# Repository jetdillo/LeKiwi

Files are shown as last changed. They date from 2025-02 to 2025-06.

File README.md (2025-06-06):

# LeKiwi
<div style="display: flex; justify-content: center; align-items: center; padding: 25px;">
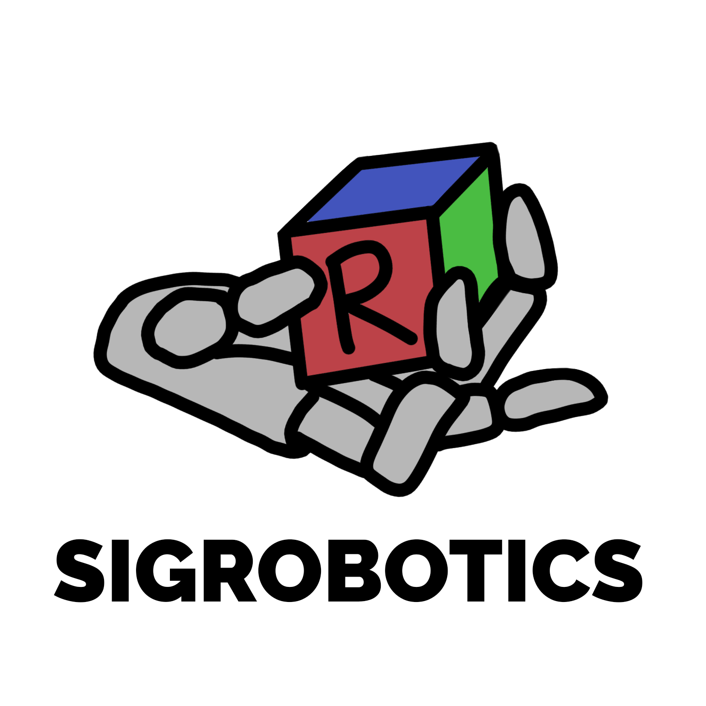
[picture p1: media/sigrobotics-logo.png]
    
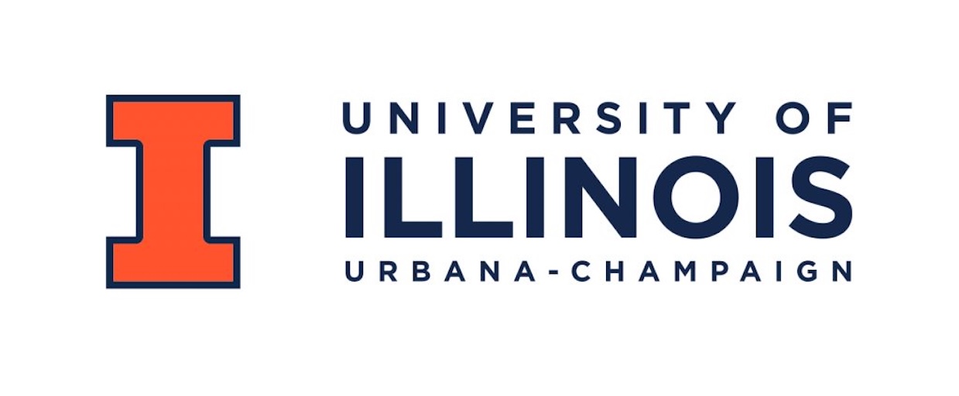
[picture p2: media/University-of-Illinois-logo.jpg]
    
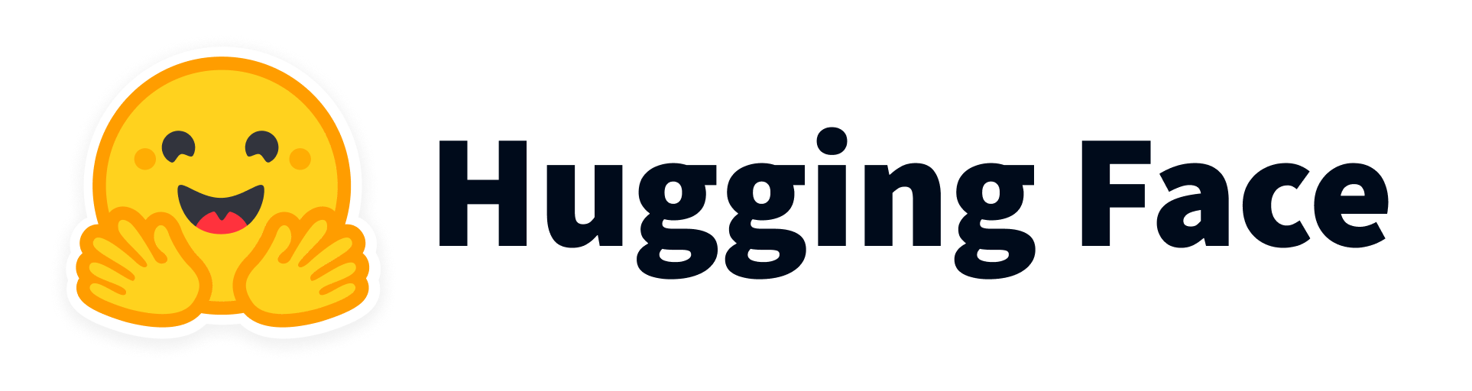
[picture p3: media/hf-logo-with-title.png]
    
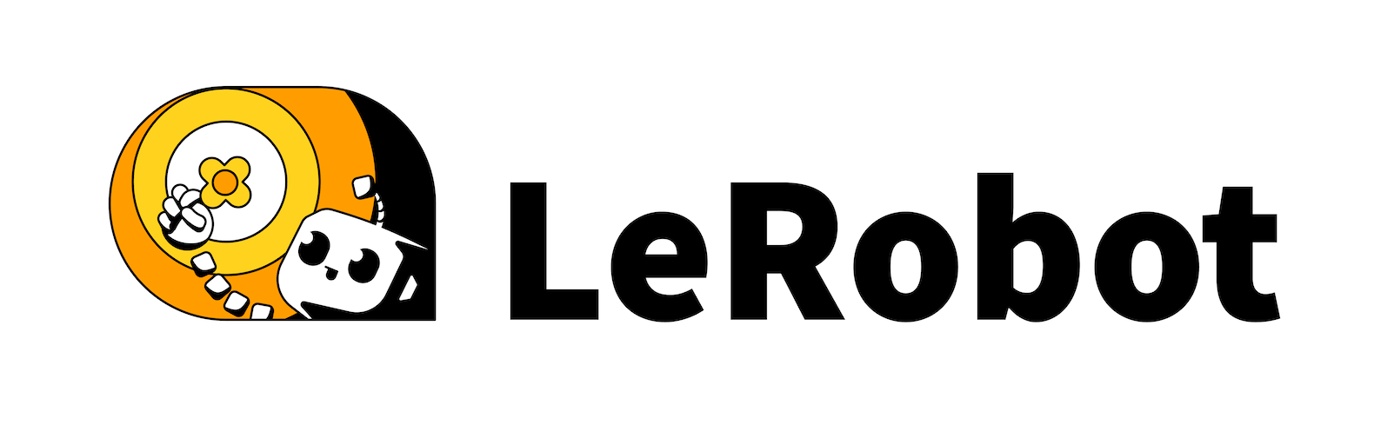
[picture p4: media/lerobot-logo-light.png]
    
</div>

> LeKiwi - Low-Cost Mobile Manipulator | Version 1

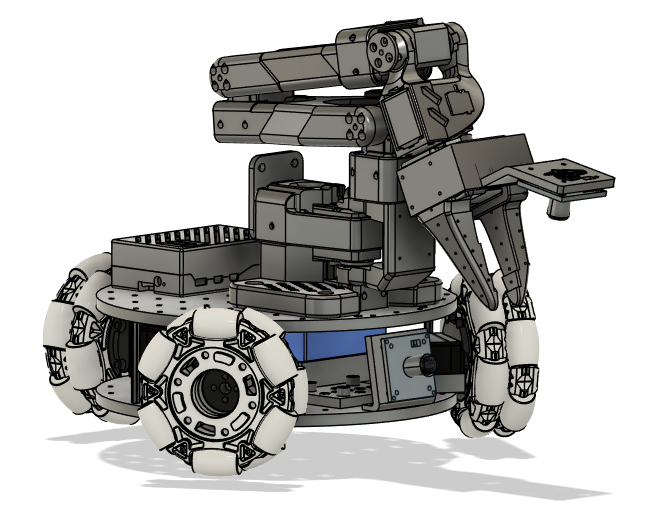
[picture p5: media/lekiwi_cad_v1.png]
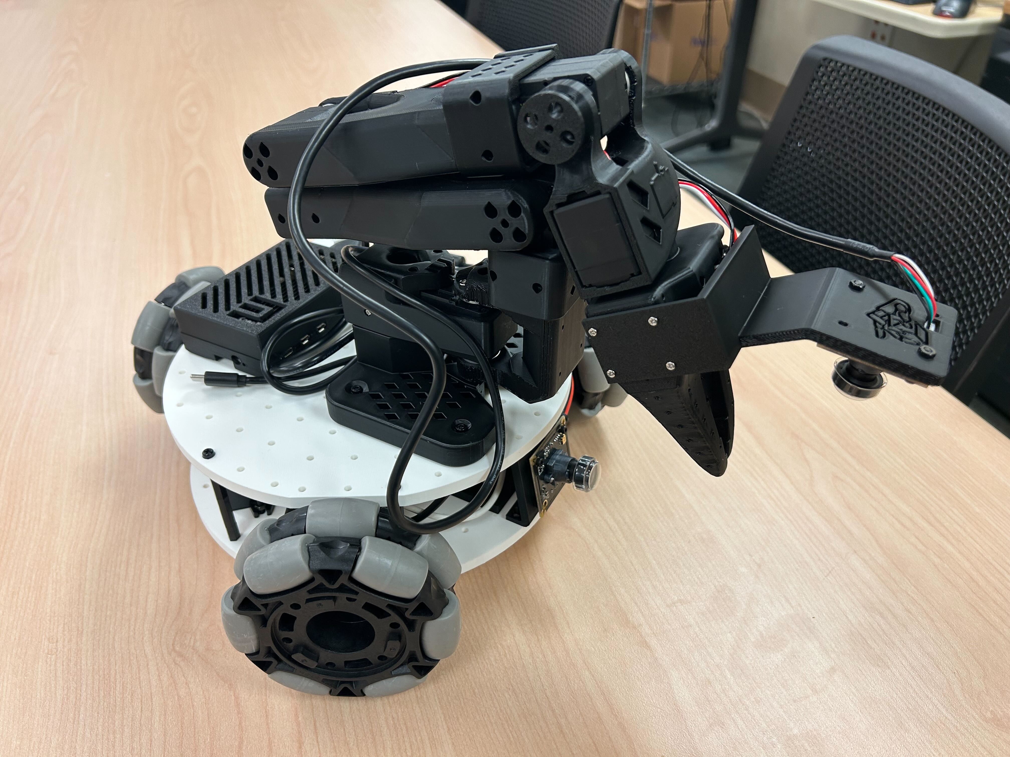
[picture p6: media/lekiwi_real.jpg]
  

## Step by step tutorial
1. [Bill of Materials](BOM.md)
2. [3D Printing](3DPrinting.md)
3. [Assembly](Assembly.md)
4. [Get started with LeRobot](https://huggingface.co/docs/lerobot/lekiwi)

## Hardware Design
#### Standardized Stacked Base Plates
- Inspired by the [open robotic platform](https://openroboticplatform.com/designrules), our base plates have 3.5mm diameter holes spaced 20mm apart for standardized mounting

#### Power
- (12V version) 12v 5A Li-ion battery
- (5V version) 65W Laptop power bank

> [!TIP]  
> If this is the first time you build robots please choose the 5V version as it’s a little bit easier to assemble. If you are more experienced and want to lift heavier objects choose the 12V version. If you want to cheapest option possible go for the wired LeKiwi version.

#### Compute
- Raspberry Pi 5
- Streaming to a Laptop

#### Drive
- 3-wheel Kiwi (holonomic) drive with omni wheels

#### Robot Arm
- [SO-ARM101](https://github.com/TheRobotStudio/SO-ARM100)

#### Sensors
- Workspace rgb camera
- Wrist rgb camera

## Software Capabilities
Goals:
- Teleoperation with controller or laptop WASD + leader arm
- Data collection pipeline
- Streaming joint angles and camera feed

## CAD Design
[Fusion 360 CAD](https://a360.co/4k1P8yO)

We also provide the [URDF](./URDF/) exported from CAD for simulation.
## Get In Touch!

Join the project on LeRobot's [Discord server](https://discord.gg/Jtz5TJtb2u) (channel `mobile-so100-arm`)! Let us know if you have any questions, suggestions, or other feedback.

## Main Contributors
Thank you to everyone who helped on the project!

**CAD Design**: Manav Chandaka, Bhargav Chandaka, Pepijn Kooijmans

**Software**: Pepijn Kooijmans, Gloria Wang, Bhargav Chandaka, Advait Patel

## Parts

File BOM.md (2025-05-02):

# Bill of Materials

This page provides a complete list of parts needed to build the LeKiwi mobile manipulator. Our total cost is displayed in the table <sup>[1](#footnote1)</sup>.

| Price| US  | EU  | CN |
|---|----:|----:|----:|
| **12V** |  **$482**  |  **€545.8**  |  **¥2891**  |
| **5V**  |  **$499**  |  **€526**  |  **¥2829**  |
| **Base only (5V)** |  **$248**  |  **€295**  |  **¥1571**  |
| **Base only (12V)** |  **$251.5**  |  **€307.8**  |  **¥1501**  |
| **Base only  wired** |  **$184**  |  **€235**  | **¥963.9**  |

> [!NOTE] 
> Prices and items may vary depending on geographic location and time of purchase. If you find links for other countries or cheaper suppliers, please create an issue or PR so that we add them to the list!

> [!IMPORTANT]  
> There are three options regarding motors and electronics (as also the case with the SO100 arms), either **5V** or **12V** or a **wired** version. If this is the first time you build robots please choose the 5V version as it’s a little bit easier to assemble. If you are more experienced and want to lift heavier objects choose the 12V version. If you want the cheapest options, go for the wired LeKiwi robot (at the end of the Bill of Materials list).

These parts are the same for both 5V and 12V versions:
### Mobile Base Structure:
| Part | Amount | Unit Cost (US) | Buy (US) | Unit Cost (EU) | Buy (EU) | Unit Cost (CN) | Buy (CN) |
| - | - | - | - | - | - | - | - |
| 4" Omni wheels | 3 | $9.99 | [VEX Robotics](https://www.vexrobotics.com/omni-wheels.html?srsltid=AfmBOorWdWT-FIiWSAbicYWSxqYr-d5X3CJSGxMkO33WO0thwlTn4DQu) | €24.5 | [RobotShop](https://eu.robotshop.com/products/100mm-omnidirectional-wheel-brass-bearing-rollers) |￥135 |[PDD](https://mobile.yangkeduo.com/goods.html?ps=kKWPC7xuzw "https://mobile.yangkeduo.com/goods.html?ps=kKWPC7xuzw")|
| M2 M3 M4 Assorted Screw Set | 1 | $14.99 | [Amazon](https://www.amazon.com/Button-Socket-Washers-Assortment-Machine/dp/B0BMQGJP3F) | €23.5 | [Amazon](https://www.amazon.fr/Cylindrique-Inoxydable-M2-Socket-Assortiment/dp/B09Y8WYFWD/) |￥25 |[Taobao（M2x5+M3套装+M3x10+M4x12）](https://e.tb.cn/h.64O1J2A9Is4pIJd "https://e.tb.cn/h.64O1J2A9Is4pIJd") |
| **Total** || **$44.96** || **€97** || **¥430** ||

### Sensors and Compute:

| Part| Amount | Unit Cost (US) | Buy (US) | Unit Cost (EU) | Buy (EU) |  Unit Cost (CN) | Buy (CN) |
|--|:-:|:-:|-|:-:|-|:-:|-|
| Raspberry Pi 5 (4GB)| 1 |$60.00| [Adafruit](https://www.adafruit.com/product/5812)| €57.00| [Mouser](https://eu.mouser.com/ProductDetail/Raspberry-Pi/SC1111?qs=HoCaDK9Nz5fnLhlMNnKTiQ%3D%3D)|￥410|[Taobao](https://e.tb.cn/h.64IIvlisvAL15g8?tk=fdOVexkHECW "https://e.tb.cn/h.64IIvlisvAL15g8?tk=fdOVexkHECW")|
| USB camera<sup>[2](#footnote2)</sup> | 2 | $12.98 | [Amazon](https://a.co/d/236G8Wn) | €12.00 | [Amazon](https://www.amazon.fr/Vinmooog-equipement-Microphone-Enregistrement-conf%C3%A9rences/dp/B0BG1YJWFN/) |￥48|[Taobao](https://e.tb.cn/h.64ILq3suMKATfUx?tk=IPSEexQAvxu "https://e.tb.cn/h.64ILq3suMKATfUx?tk=IPSEexQAvxu")|
| microSD card | 1 | $11.23 | [Amazon](https://www.amazon.com/SanDisk-Extreme-microSDXC-Memory-Adapter/dp/B09X7C7LL1/) | €10.00 | [Amazon](https://www.amazon.fr/Lexar-Carte-Micro-adaptateur-Smartphone/dp/B08XZ2KS1F)|￥58|[Taobao](https://e.tb.cn/h.64DMZzLz5h26s12?tk=eImPex96lCQ "https://e.tb.cn/h.64DMZzLz5h26s12?tk=eImPex96lCQ")|
| **Total** ||  **$98**  ||  **€91** ||  **¥564** ||

### Other
| Part| Amount | Unit Cost (US) | Buy (US) | Unit Cost (EU) | Buy (EU) | Unit Cost (CN) | Buy (CN) |
|--|:-:|:-:|-|:-:|-|:-:|-|
| Table Clamp 4pcs | 1 | $18 | [Amazon](https://www.amazon.com/WORKPRO-Clamps-Woodworking-One-Handed-Spreader/dp/B0CQYDJWS8/) | € 21 | [Amazon](https://www.amazon.fr/dp/B08HW9VFM8/)| ¥10.8\*4  |[Taobao](https://e.tb.cn/h.64r5eomI6L59tBE?tk=gZWeex9fnlB "https://e.tb.cn/h.64r5eomI6L59tBE?tk=gZWeex9fnlB")|
| Screwdriver Set | 1 | $6 | [Amazon](https://www.amazon.com/Precision-Phillips-Screwdriver-Electronics-Computer/dp/B0DB227RTH) | €10 | [Amazon](https://www.amazon.fr/dp/B08ZXVMVYD/) | ￥20 |[Taobao](https://e.tb.cn/h.6ReL0wwgtPuSmNV?tk=3rLDV10AVtr)  |
| USB-C to USB-A Cable 2 pcs | 1 | $7 | [Amazon](https://www.amazon.com/Charging-etguuds-Charger-Braided-Compatible/dp/B0B8NWLLW2/?th=1) | €7 | [Amazon](https://www.amazon.fr/dp/B07BNF842T/) |￥17  |[Taobao](https://e.tb.cn/h.64HOv24RLmYC4Yh?tk=AXpgexkDFd4 "https://e.tb.cn/h.64HOv24RLmYC4Yh?tk=AXpgexkDFd4")|
| **Total** ||  **$31**  ||  **€38** || **¥80.20** ||

## 12V version :battery:

### Mobile Base Electronics (12V):
| Part | Amount | Unit Cost (US) | Buy (US) | Unit Cost (EU) | Buy (EU) | Unit Cost (CN) | Buy (CN) |
|:---|:---:|:---:|:---|:---:|---:|:-:|-|
| 12v 5a Battery | 1 | $32.99 | [Amazon](https://www.amazon.com/KBT-Rechargeable-Connector-Replacement-Security/dp/B0C242DYT1/ref=sr_1_2_sspa?) | €45.79 | [Amazon](https://www.amazon.fr/dp/B0D5QSMW21) | ￥70 |[Taobao](https://e.tb.cn/h.64IJNTnXwhn44BS?tk=PQQ8exkJEtR "https://e.tb.cn/h.64IJNTnXwhn44BS?tk=PQQ8exkJEtR")|
| Lever Wire Connector | 1 | $6.70 | [Amazon](https://www.amazon.com/Wago-221-413-LEVER-NUTS-Conductor-Connectors/dp/B06XGYXVXR/ref=sr_1_4) | €7.18 | [Amazon](https://www.amazon.fr/221-413-fil-électrique-connecteur-220-240-Terminal/dp/B01AKF3I58) | ￥3.50 |[Taobao](https://e.tb.cn/h.64r0Z6Y5jZczq5q?tk=XEaSex908q0 "https://e.tb.cn/h.64r0Z6Y5jZczq5q?tk=XEaSex908q0")|
| 12v 5a DC plug connector | 1 | $9.49 | [Amazon](https://www.amazon.com/43x2pcs-Connectors-Security-Lighting-MILAPEAK/dp/B072BXB2Y8/ref=sr_1_11) | €8.99 | [Amazon](https://www.amazon.fr/RUNCCI-YUN-Alimentation-dalimentation-Connecteur-Surveiller/dp/B0CX44HTKZ) | ￥3.10 |[Taobao](https://e.tb.cn/h.64IFOvrMdUVoQQX?tk=nahtexkvokE "https://e.tb.cn/h.64IFOvrMdUVoQQX?tk=nahtexkvokE")|
| 12v to 5v 5a USB-C converter | 1 | $9.99 | [Amazon](https://www.amazon.com/Klnuoxj-Converter-Interface-Waterproof-Compatible/dp/B0CRVW7N2J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) | €9.99 | [Amazon](https://www.amazon.fr/Greluma-convertisseur-Adaptateur-dalimentation-Compatible/dp/B0D7VDL2X6) | ￥20 |[1688](https://qr.1688.com/s/Eb6ykv4y "https://qr.1688.com/s/Eb6ykv4y") |
| 12v ST3215 Feetech Servo | 3 | $13.89 | [Alibaba](https://www.alibaba.com/product-detail/Feetech-STS3215-SO-ARM100-Servo-12V_1601292634404.html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) | €13.38 | [Alibaba](https://www.alibaba.com/product-detail/Feetech-STS3215-SO-ARM100-Servo-12V_1601292634404.html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)  | ￥110 |[Taobao](https://e.tb.cn/h.64H9u3maGWzIp5Q?tk=T5liexkG6Yz "https://e.tb.cn/h.64H9u3maGWzIp5Q?tk=T5liexkG6Yz")|
| **Total** | | **$108.5** | | **€118.8** | | **￥426.60** | |

### SO-101 2 Robot Arm Teleoperation Set (12V):
| Part | Amount | Unit Cost (US) | Buy (US) | Unit Cost (EU) | Buy (EU) | Unit Cost (CN) | Buy (CN) |
|:---|:---:|:---:|:---|:---:|---:|:-:|-|
| 12v ST3215 Servo | 12 | $13.89 | [Alibaba](https://www.alibaba.com/product-detail/Feetech-STS3215-SO-ARM100-Servo-12V_1601292634404.html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) | €13.38 | [Alibaba](https://www.alibaba.com/product-detail/Feetech-STS3215-SO-ARM100-Servo-12V_1601292634404.html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) | ￥110  |[Taobao](https://e.tb.cn/h.64H9u3maGWzIp5Q?tk=T5liexkG6Yz "https://e.tb.cn/h.64H9u3maGWzIp5Q?tk=T5liexkG6Yz")|
| Motor Control Board | 2 | $10.55 | [Amazon](https://www.amazon.com/Waveshare-Integrates-Control-Circuit-Supports/dp/B0CTMM4LWK/) | €12.00 | [Amazon](https://www.amazon.fr/Waveshare-Integrates-Control-Applicable-Integrate/dp/B0CJ6TP3TP) | ￥24 |[Taobao](https://e.tb.cn/h.64DOUpLpB5crVdH?tk=BSaTex9UHWj "https://e.tb.cn/h.64DOUpLpB5crVdH?tk=BSaTex9UHWj")|
| Power Supply | 1 | $12 | [Amazon](https://www.amazon.com/ALITOVE-Adapter-Converter-100-240V-5-5x2-1mm/dp/B01GEA8PQA) | €15 | [Amazon](https://www.amazon.fr/LEDMO-Alimentation-Adaptateur-Transformateurs-Chargeur/dp/B07PGLXK4X) | ￥22  |[Taobao](https://e.tb.cn/h.64D9xUuAdpkswUx?tk=JRRwex94phr "https://e.tb.cn/h.64D9xUuAdpkswUx?tk=JRRwex94phr")|
| **Total** | | **$199.78** | | **€199.56** | | **￥1,390** | |

## 5V version :battery:

### Mobile Base Electronics (5V):
| Part | Amount | Unit Cost (US) | Buy (US) | Unit Cost (EU) | Buy EU |  Unit Cost (CN) | Buy (CN) |
|:---|:---:|:---:|:---:|:---:|:---|:-:|-|
| 20000maH 85W Power Bank | 1 | $42 | [Amazon](https://www.amazon.com/CUKTECH-20000mAh-Portable-Charging-External/dp/B0D3PMWN46/) | €50 | [Amazon](https://www.amazon.fr/CUKTECH-Batterie-Affichage-Numérique-Compatible/dp/B0D3PMWN46/) | ￥178 |[Taobao](https://e.tb.cn/h.6RhPvaQ2zjEEjQ1?tk=WDDkV1XzVBM) 
| STS3215 Servo | 3 | $15 | [Alibaba](https://www.alibaba.com/product-detail/6PCS-7-4V-STS3215-Servos-for_1600523509006.html) | 13€ | [Alibaba](https://www.alibaba.com/product-detail/6PCS-7-4V-STS3215-Servos-for_1600523509006.html) | ￥99  |[Taobao](https://e.tb.cn/h.6RhJCXsXFrqIabq?tk=ve0EV12Wg26)|
| USB-C Cable 2pcs (1feet/0.5 m) | 1 | $8 | [Amazon](https://www.amazon.com/INIU-2-Pack-iPhone-Samsung-MacBook/dp/B0D8QBHZSW/) | €7.6 | [Amazon](https://www.amazon.fr/SUNGUY-charge-rapide-MacBook-Samsung/dp/B0DNM89Q5P) | ¥9.4\*2 |[Taobao](https://e.tb.cn/h.6R5fJaBv1I46QUx?tk=2b5IV1XKMq7) |
| USB-C To DC Cable | 1 | $10 | [Amazon](https://www.amazon.com/DSD-TECH-MagicConn-Power-Cable/dp/B0B9G1KFL3) | €10 | [Amazon](https://www.amazon.fr/dp/B0B9G1KFL3) |￥3 |[Taobao](https://e.tb.cn/h.6R21AdjEPDkfw2R?tk=qmTmV1Xx2Pg) |
| **Total** | | **$105** | | **€106.6** | | **￥496.80** | |

### SO-101 2 Robot Arm Teleoperation Set (5V):
| Part | Amount | Unit Cost (US) | Buy US | Unit Cost (EU) | Buy EU |  Unit Cost (CN) | Buy (CN) |
|---|---|---|---|---|---|---|---|
| STS3215 Servo | 12 | $15 | [Alibaba](https://www.alibaba.com/product-detail/6PCS-7-4V-STS3215-Servos-for_1600523509006.html) | €13 | [Alibaba](https://www.alibaba.com/product-detail/6PCS-7-4V-STS3215-Servos-for_1600523509006.html) | ￥99  |[Taobao](https://e.tb.cn/h.6RhJCXsXFrqIabq?tk=ve0EV12Wg26)|
| Motor Control Board | 2 | $11 | [Amazon](https://www.amazon.com/Waveshare-Integrates-Control-Circuit-Supports/dp/B0CTMM4LWK/) | €12 | [Amazon](https://www.amazon.fr/-/en/dp/B0CJ6TP3TP/)|  ￥24 |[Taobao](https://e.tb.cn/h.64DOUpLpB5crVdH?tk=BSaTex9UHWj "https://e.tb.cn/h.64DOUpLpB5crVdH?tk=BSaTex9UHWj")|
| Power Supply | 1 | $10 | [Amazon](https://www.amazon.com/Facmogu-Switching-Transformer-Compatible-5-5x2-1mm/dp/B087LY41PV/) | €13 | [Amazon](https://www.amazon.fr/-/en/dp/B01HRR9GY4/) | ￥22  |[Taobao](https://e.tb.cn/h.64D9xUuAdpkswUx?tk=JRRwex94phr "https://e.tb.cn/h.64D9xUuAdpkswUx?tk=JRRwex94phr")|
| **Total** | | **$212** | | **€193** | | **¥1258** | |

## Wired version :electric_plug:
Everything needed for the wired version:

| Part | Amount | Unit Cost (US) | Buy (US) | Unit Cost (EU) | Buy (EU) | Unit Cost (CN) | Buy (CN) |
| - | - | - | - | - | - |- | - |
| 4" Omni wheels | 3 | $9.99 | [VEX Robotics](https://www.vexrobotics.com/omni-wheels.html?srsltid=AfmBOorWdWT-FIiWSAbicYWSxqYr-d5X3CJSGxMkO33WO0thwlTn4DQu) | €24.5 | [RobotShop](https://eu.robotshop.com/products/100mm-omnidirectional-wheel-brass-bearing-rollers) |￥135 |[PDD](https://mobile.yangkeduo.com/goods.html?ps=kKWPC7xuzw "https://mobile.yangkeduo.com/goods.html?ps=kKWPC7xuzw")|
| M2 M3 M4 Assorted Screw Set | 1 | $14.99 | [Amazon](https://www.amazon.com/Button-Socket-Washers-Assortment-Machine/dp/B0BMQGJP3F) | €23.5 | [Amazon](https://www.amazon.fr/Cylindrique-Inoxydable-M2-Socket-Assortiment/dp/B09Y8WYFWD/) |￥25 |[Taobao（M2x5+M3套装+M3x10+M4x12）](https://e.tb.cn/h.64O1J2A9Is4pIJd "https://e.tb.cn/h.64O1J2A9Is4pIJd") |
| USB camera<sup>[2](#footnote2)</sup> | 2 | $12.98 | [Amazon](https://a.co/d/236G8Wn) | €12.00 | [Amazon](https://www.amazon.fr/Vinmooog-equipement-Microphone-Enregistrement-conf%C3%A9rences/dp/B0BG1YJWFN/) |￥48|[Taobao](https://e.tb.cn/h.64ILq3suMKATfUx?tk=IPSEexQAvxu "https://e.tb.cn/h.64ILq3suMKATfUx?tk=IPSEexQAvxu")|
| USB-C to USB-A Cable 2 pcs | 1 | $7 | [Amazon](https://www.amazon.com/Charging-etguuds-Charger-Braided-Compatible/dp/B0B8NWLLW2/?th=1) | €7 | [Amazon](https://www.amazon.fr/dp/B07BNF842T/) |￥17  |[Taobao](https://e.tb.cn/h.64HOv24RLmYC4Yh?tk=AXpgexkDFd4 "https://e.tb.cn/h.64HOv24RLmYC4Yh?tk=AXpgexkDFd4")|
| USB-C To DC Cable | 1 | $10 | [Amazon](https://www.amazon.com/DSD-TECH-MagicConn-Power-Cable/dp/B0B9G1KFL3) | €10 | [Amazon](https://www.amazon.fr/dp/B0B9G1KFL3) |￥3 |[Taobao](https://e.tb.cn/h.6R21AdjEPDkfw2R?tk=qmTmV1Xx2Pg) |
| STS3215 Servo | 3 | $15 | [Alibaba](https://www.alibaba.com/product-detail/6PCS-7-4V-STS3215-Servos-for_1600523509006.html) | €13 | [Alibaba](https://www.alibaba.com/product-detail/6PCS-7-4V-STS3215-Servos-for_1600523509006.html) | ￥99  |[Taobao](https://e.tb.cn/h.6RhJCXsXFrqIabq?tk=ve0EV12Wg26)|
| Motor Control Board | 1 | $11 | [Amazon](https://www.amazon.com/Waveshare-Integrates-Control-Circuit-Supports/dp/B0CTMM4LWK/) | €12 | [Amazon](https://www.amazon.fr/-/en/dp/B0CJ6TP3TP/)|  ￥24 |[Taobao](https://e.tb.cn/h.64DOUpLpB5crVdH?tk=BSaTex9UHWj "https://e.tb.cn/h.64DOUpLpB5crVdH?tk=BSaTex9UHWj")|
| Power Supply | 1 | $10 | [Amazon](https://www.amazon.com/Facmogu-Switching-Transformer-Compatible-5-5x2-1mm/dp/B087LY41PV/) | €13 | [Amazon](https://www.amazon.fr/-/en/dp/B01HRR9GY4/) | ￥22  |[Taobao](https://e.tb.cn/h.64D9xUuAdpkswUx?tk=JRRwex94phr "https://e.tb.cn/h.64D9xUuAdpkswUx?tk=JRRwex94phr")|
| USB Hub | 1 | $16 | [Amazon](https://www.amazon.com/UGREEN-Delivery-Multiport-Adapter-Thinkpad/dp/B0BR3M8XHK) | €14 | [Amazon](https://www.amazon.fr/UGREEN-Revodok-Alimenté-Adaptateur-Compatible/dp/B0BR3M8XHK) | ¥49.9 | [Taobao](https://e.tb.cn/h.6R2AeZgsSjchx0Z?tk=VTQMV12rt11) |
| USB-C extension cable | 1 | $13.99 | [Amazon](https://www.amazon.com/Extension-Extender-Transfer-AINOPE-Compatible/dp/B0BHHK1W95/) | €19 | [Amazon](https://www.amazon.fr/EUDOBEL-Rallonge-Extension-Thunderbolt-iPhone16/dp/B0DLP16V7J/) | ¥25 | [Taobao](https://e.tb.cn/h.6RdbxakOTokPM0X?tk=nMrBV12F4uI ) |
| **Total** || **$184** || **€235** || **¥963.9** ||

> Head to [3D Printing](3DPrinting.md) for the next step!

<br></br>

## Footnotes
<a name="footnote1">1</a>: Doesn't include cost of 3D printing

<a name="footnote2">2</a>: Another supported camera option is the Arducam 5MP Wide Angle found [here](https://www.amazon.com/Arducam-Camera-Computer-Without-Microphone/dp/B0972KK7BC)

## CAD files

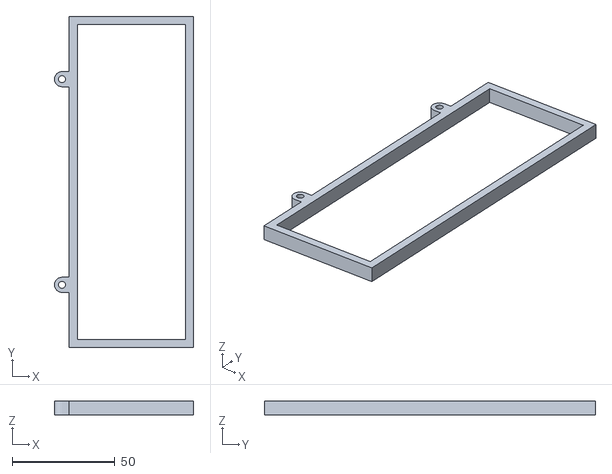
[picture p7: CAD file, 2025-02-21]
3DPrintMeshes/5v_specific/5v_power_bank_holder.stl
67.7 x 161.0 x 7.00

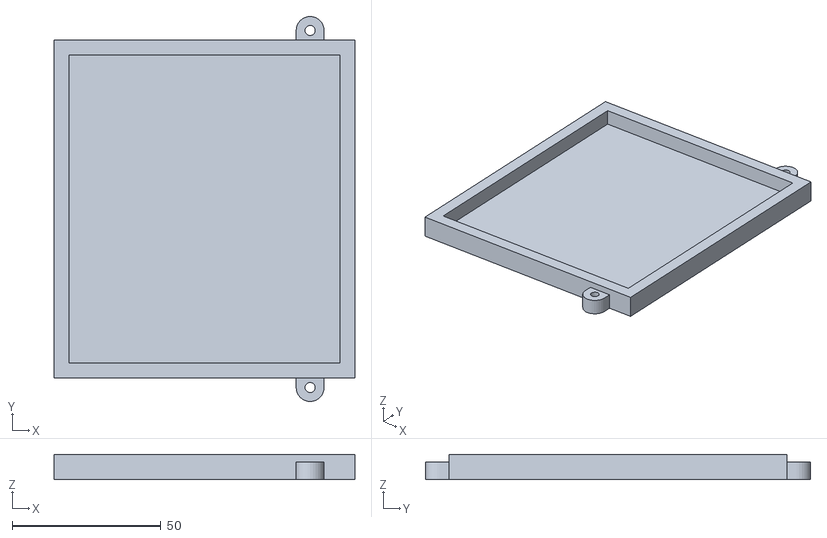
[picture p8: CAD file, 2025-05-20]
3DPrintMeshes/jetson_holder.stl
101.0 x 129.4 x 8.50

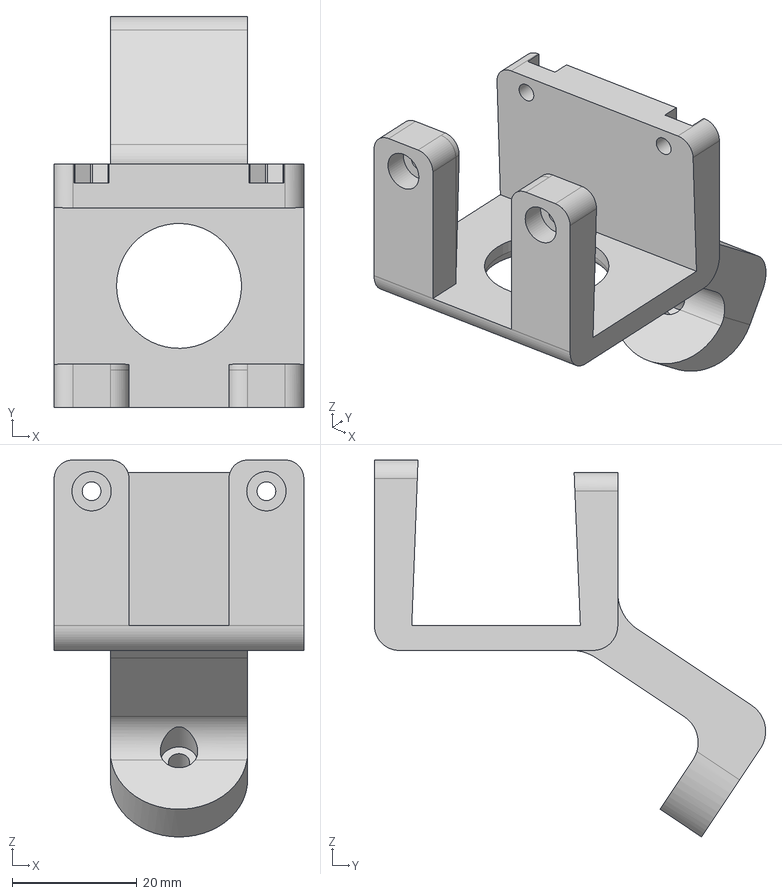
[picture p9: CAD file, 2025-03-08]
3DPrintMeshes/webcam_mount/webcam_mount_wrist.step
40.0 x 62.7 x 60.4 mm

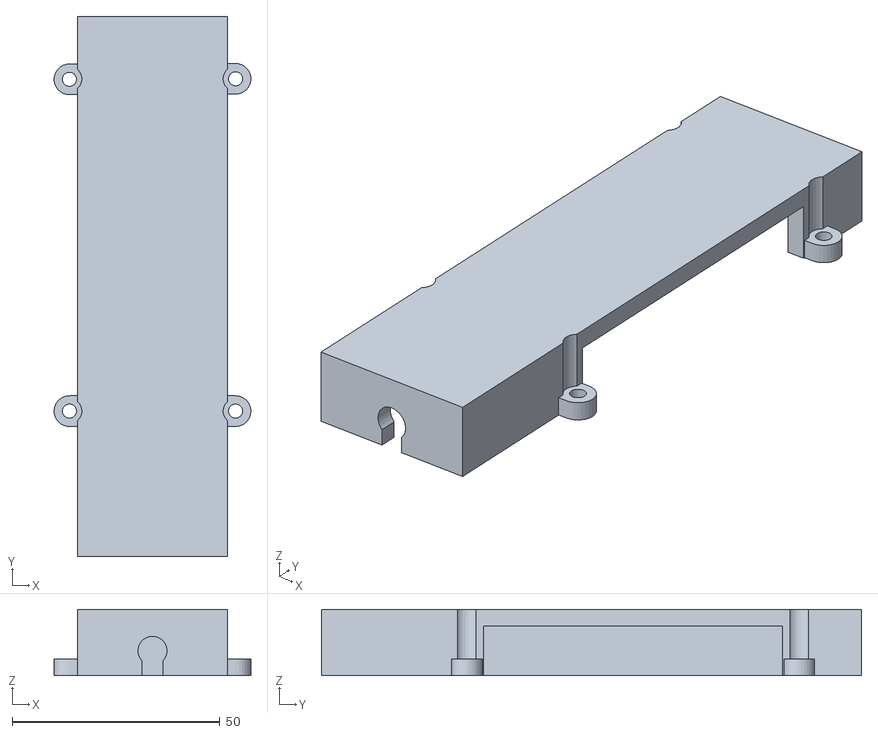
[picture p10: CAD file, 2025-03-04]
3DPrintMeshes/wired_specific/usb_connector_case v1.stl
47.4 x 130.0 x 16.0

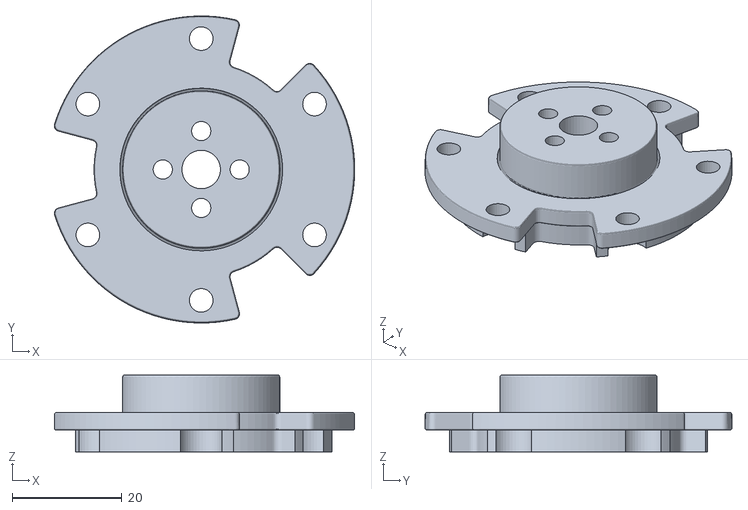
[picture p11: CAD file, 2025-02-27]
URDF/meshes/omni_wheel_mount-v5-1.stl
54.7 x 55.9 x 14.0

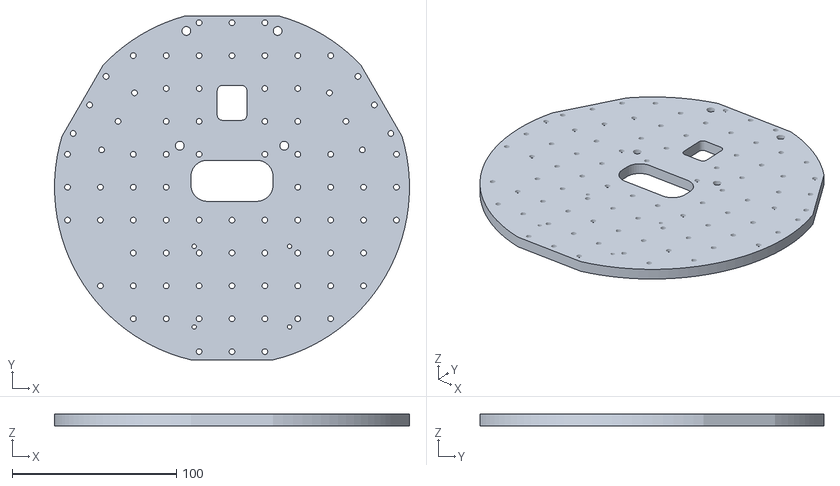
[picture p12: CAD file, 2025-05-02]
3DPrintMeshes/base_plate_layer2.stl
215.9 x 209.0 x 7.00

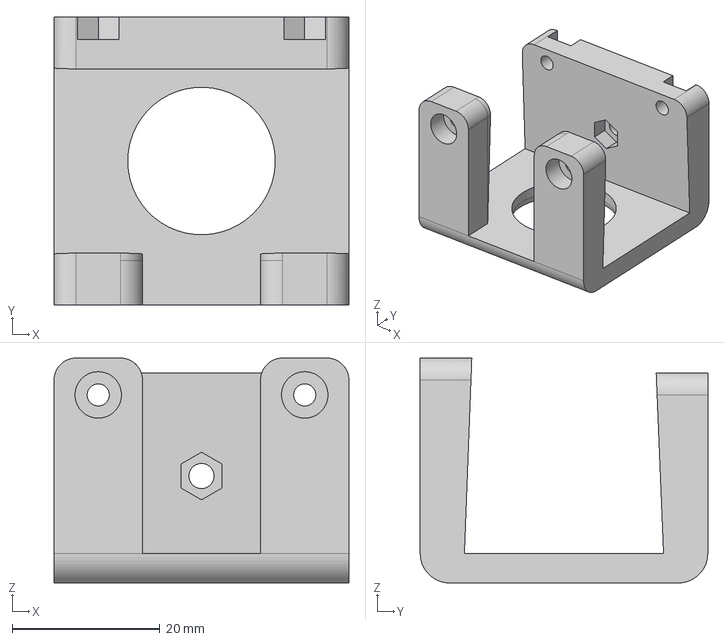
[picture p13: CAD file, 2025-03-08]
3DPrintMeshes/webcam_mount/webcam_mount.step
40.0 x 39.0 x 30.5 mm

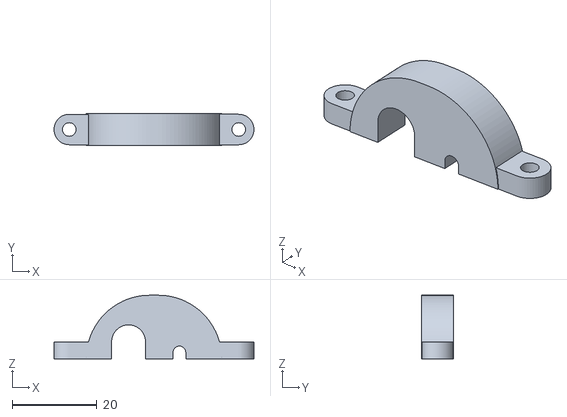
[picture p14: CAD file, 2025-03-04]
3DPrintMeshes/wired_specific/cable_holder v0.stl
47.2 x 7.50 x 15.0

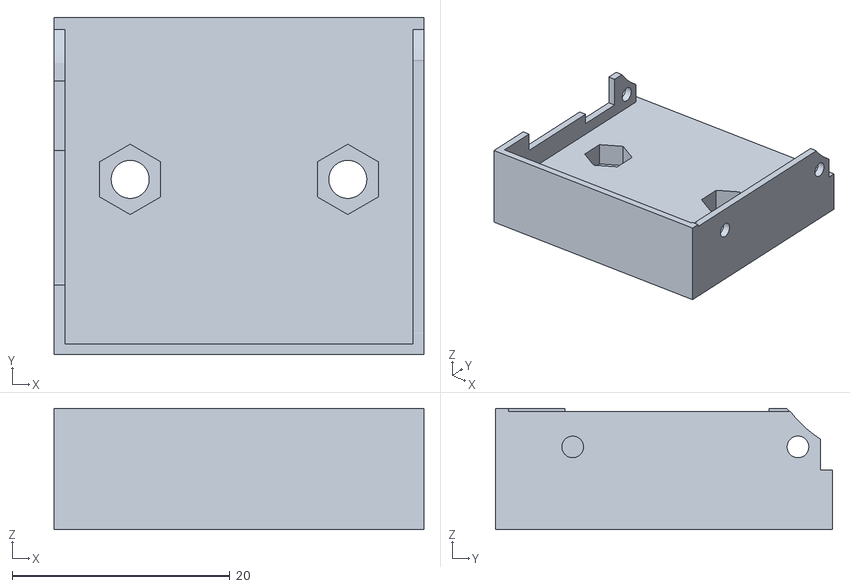
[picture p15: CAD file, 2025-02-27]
URDF/meshes/drive_motor_mount-v11-2.stl
34.0 x 31.0 x 11.2

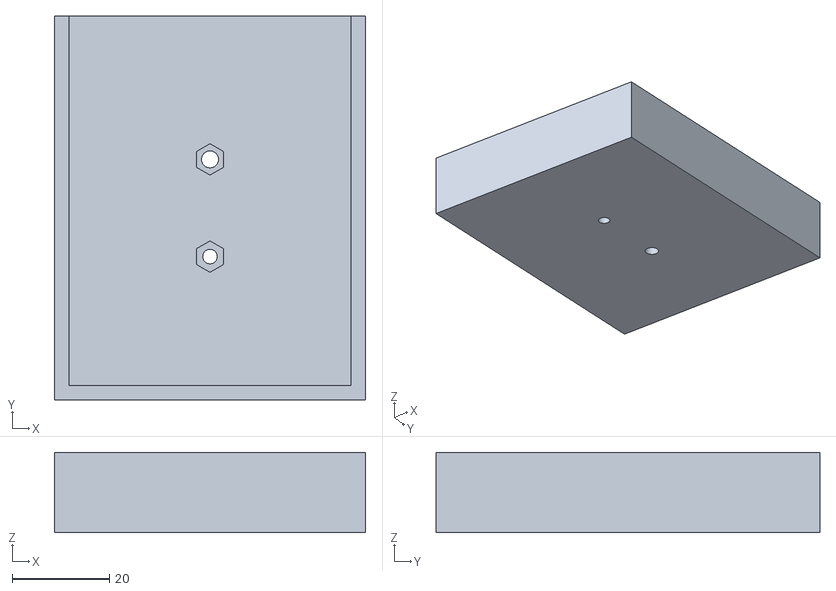
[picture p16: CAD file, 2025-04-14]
3DPrintMeshes/battery_mount_eu.stl
64.0 x 79.0 x 16.5

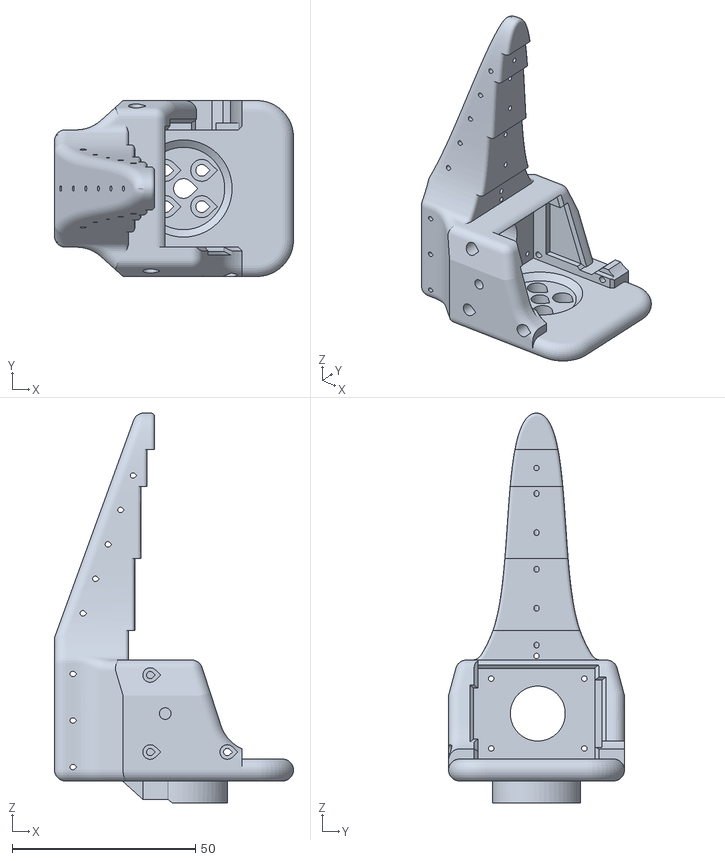
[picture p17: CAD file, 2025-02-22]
3DPrintMeshes/webcam_mount/so100_gripper_cam_mount_insert.stl
65.2 x 48.0 x 106.4

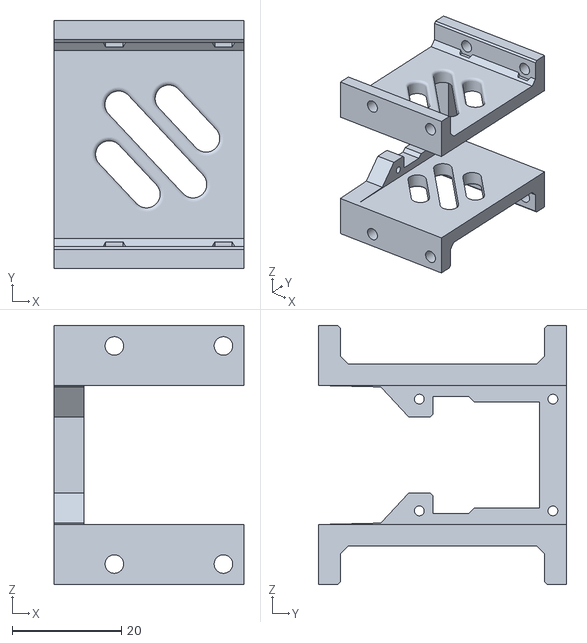
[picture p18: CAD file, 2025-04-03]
3DPrintMeshes/drive_motor_mount_v2.stl
34.8 x 45.5 x 47.5

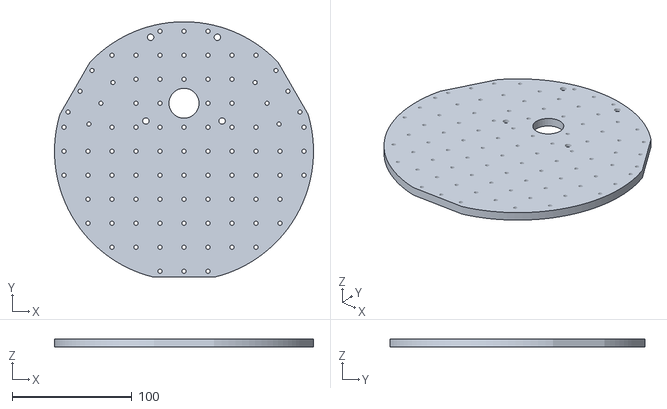
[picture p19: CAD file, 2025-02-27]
URDF/meshes/base_plate_layer2-v3.stl
215.9 x 212.9 x 7.00

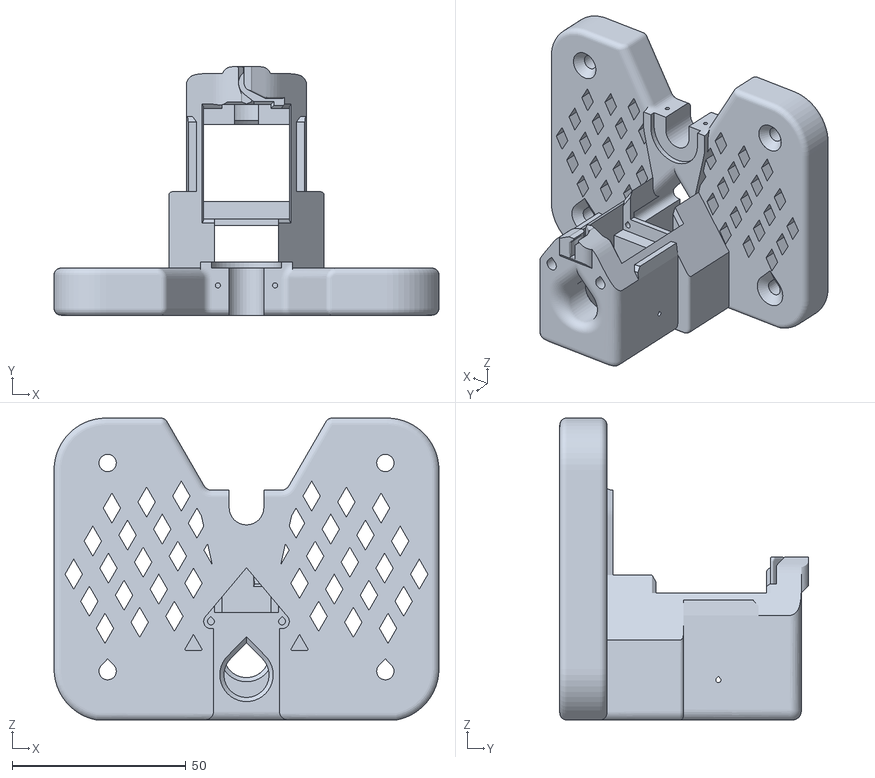
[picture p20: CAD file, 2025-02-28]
3DPrintMeshes/modified_base_arm.stl
110.9 x 71.6 x 87.0

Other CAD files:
3DPrintMeshes/wrist_camera_mount.stl
URDF/meshes/lipo_battery_mount-v3.stl
3DPrintMeshes/base_plate_layer1.stl
3DPrintMeshes/battery_mount.stl
3DPrintMeshes/drive_motor_mount.stl
3DPrintMeshes/pi_case_bottom.stl
3DPrintMeshes/pi_case_top.stl
3DPrintMeshes/servo_wheel_hub.stl
3DPrintMeshes/webcam_mount/webcam_mount.stl
3DPrintMeshes/webcam_mount/webcam_mount_wrist.stl
URDF/meshes/94868A713_NO-THREADS_Female-Threaded-Hex-Standoff-1.stl
URDF/meshes/94868A713_NO-THREADS_Female-Threaded-Hex-Standoff-2.stl
URDF/meshes/94868A713_NO-THREADS_Female-Threaded-Hex-Standoff-3.stl
URDF/meshes/94868A713_NO-THREADS_Female-Threaded-Hex-Standoff-4.stl
URDF/meshes/94868A713_NO-THREADS_Female-Threaded-Hex-Standoff-5.stl
URDF/meshes/94868A713_NO-THREADS_Female-Threaded-Hex-Standoff.stl
URDF/meshes/Base_08q-v1.stl
URDF/meshes/Battery---Battery-5.2-Ah-DC5521-Plug-v2.stl
URDF/meshes/Bottom-V2-v3.stl
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

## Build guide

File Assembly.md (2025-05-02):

# Assembly
> **Estimated time:** 2 hours

*Exact component placements can be visualized in the [Fusion360 Online CAD](https://a360.co/4k1P8yO)*

*We assume you already have a [SO-100/SO-101 Arm](https://github.com/TheRobotStudio/SO-ARM100) built*
### 1. Assemble Wheel Modules (3 per robot)

1. Attach the drive motor to the motor mount using 4 m2x5 tap screws.

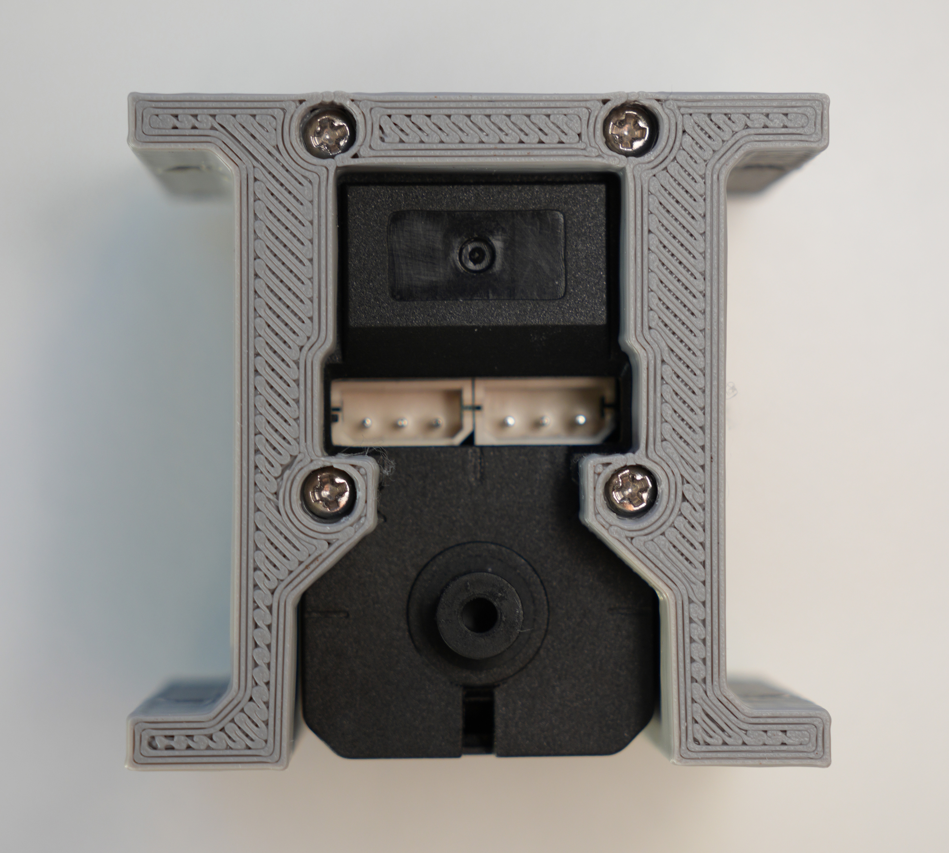
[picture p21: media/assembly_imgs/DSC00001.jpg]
    

2. Screw the drive motor mount onto the bottom base plate using 4 m3x12 machine screws.

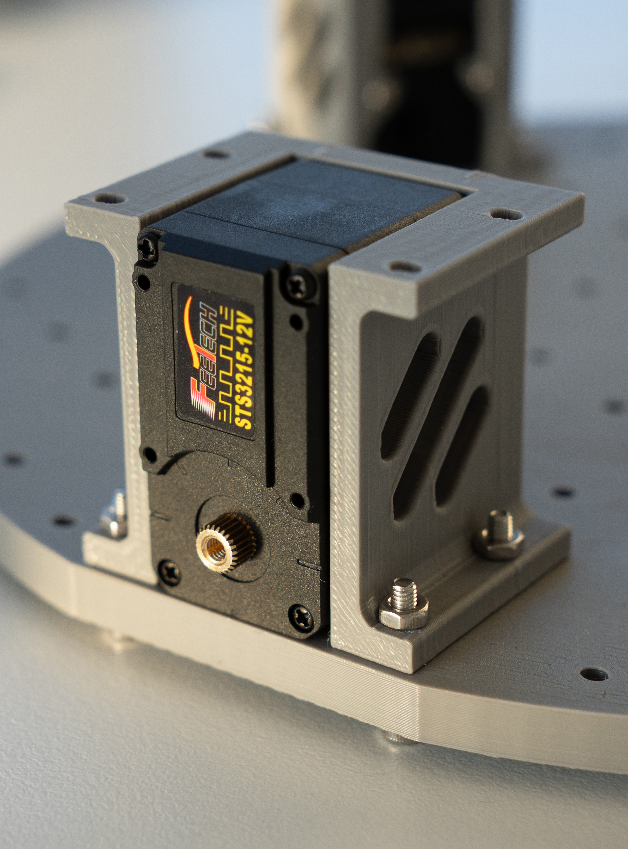
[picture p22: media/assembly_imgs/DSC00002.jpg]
    

3. Attach the wheel hub to the omniwheel using 2 m4x12 machine screws.

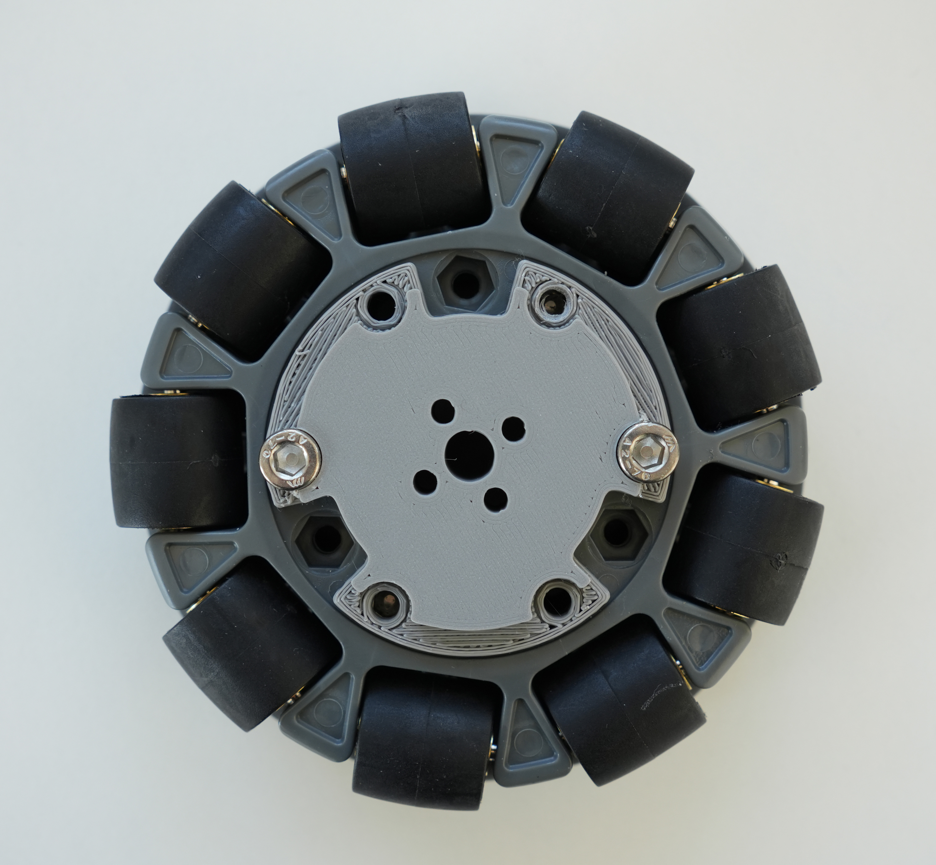
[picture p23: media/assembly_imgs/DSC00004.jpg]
    

4. Attach the servo horn to the wheel hub using 2 m3x16 machine screws.

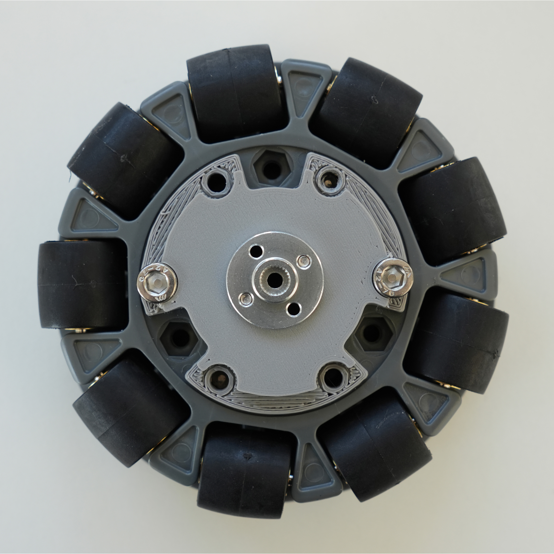
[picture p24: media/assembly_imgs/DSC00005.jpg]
    
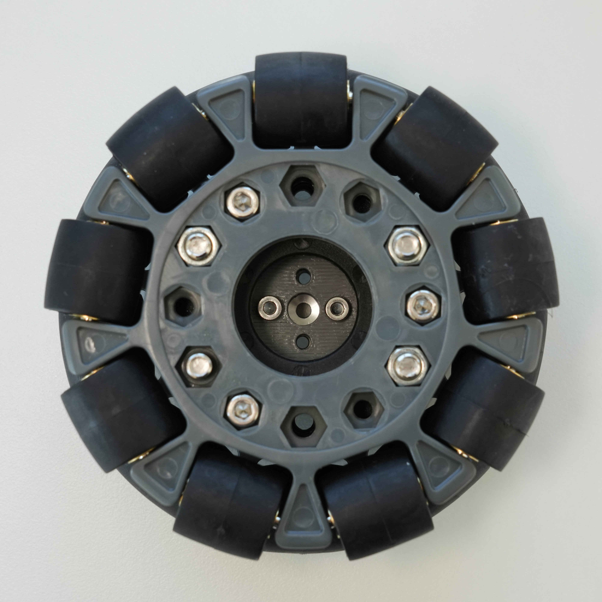
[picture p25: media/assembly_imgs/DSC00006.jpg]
    

5. Attach the servo horn to the drive motor using 1 m3x6 machine screw.

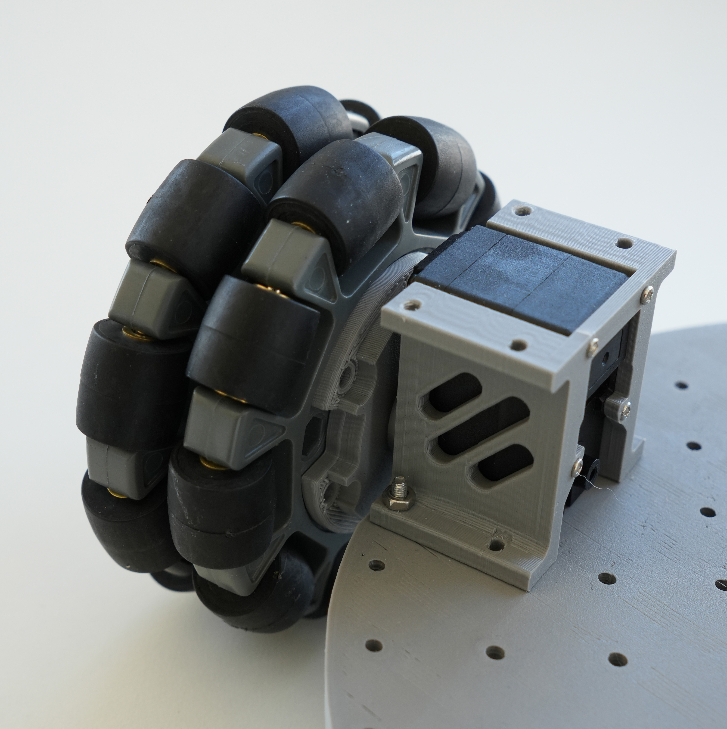
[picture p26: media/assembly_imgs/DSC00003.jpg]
    

With all 3 modules attached to the bottom base plate:

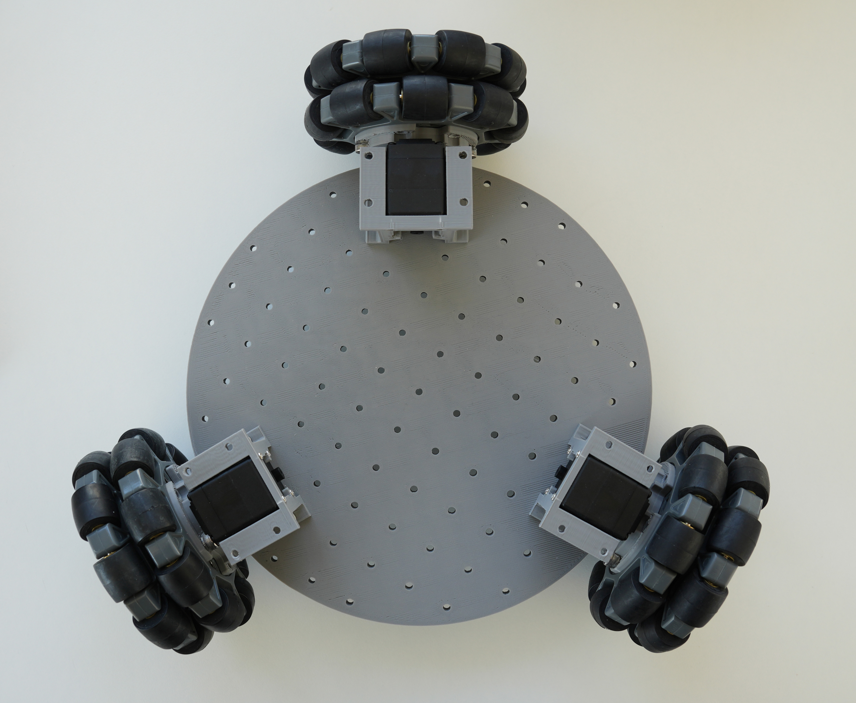
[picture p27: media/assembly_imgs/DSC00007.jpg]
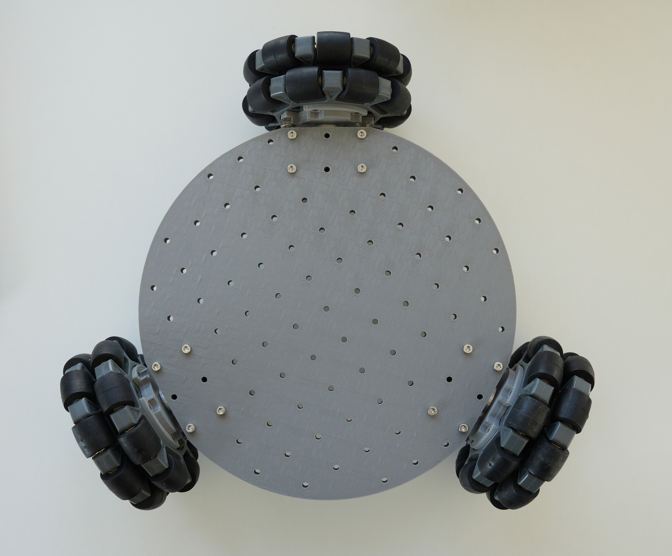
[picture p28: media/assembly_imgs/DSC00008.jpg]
 

### 2. Bottom Plate Assembly
1. Insert m3 nuts into the mounts for the servo controller and battery mounts. Screw both onto the bottom base plate with 4 m3x12 machine screws.

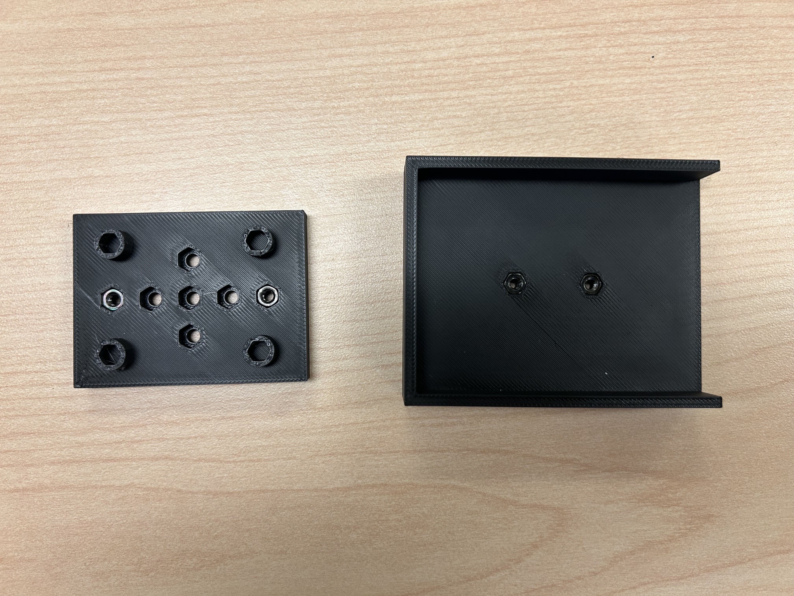
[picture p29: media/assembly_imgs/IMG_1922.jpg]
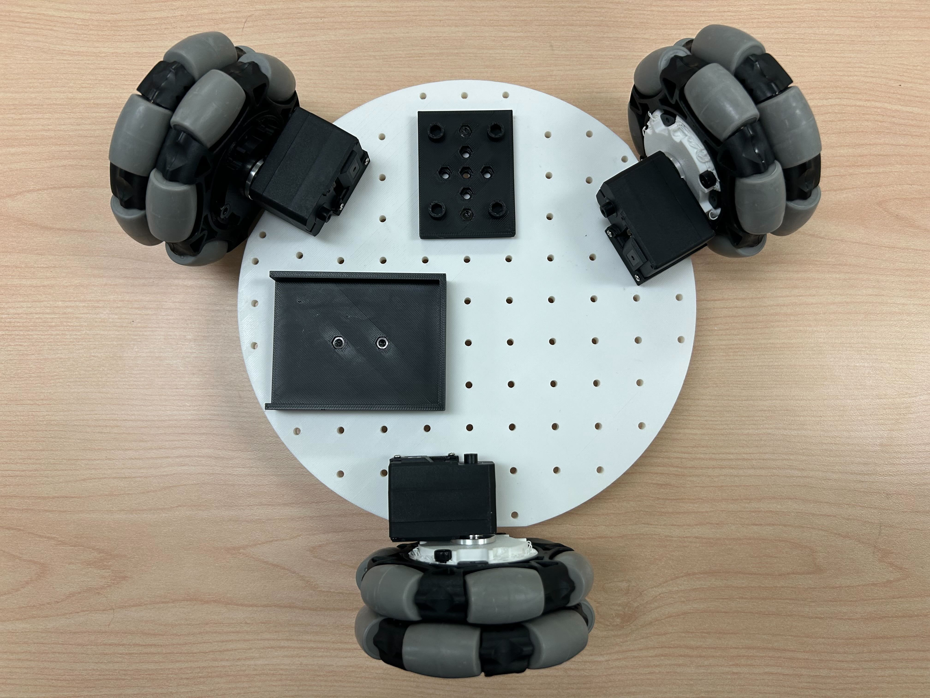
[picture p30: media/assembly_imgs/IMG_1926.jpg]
     
2. Add the servo driver and attach the wires to the 3 drive servos.

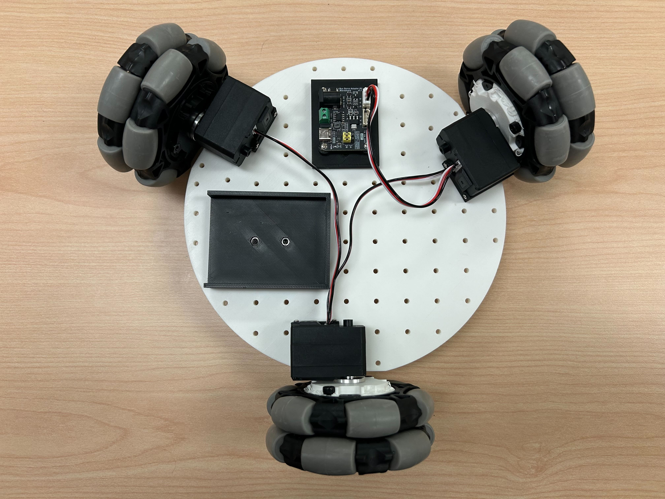
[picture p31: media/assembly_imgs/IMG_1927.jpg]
    
3. Wiring Electronics
   - For the **12V version**: 
   Use the wago lever connectors to connect the ground and power battery wire leads to the leads of the 12v->5v converter and the dc barrel plug adapter. Screw on the 12v to 5v converter to the bottom base plate with 2 m3x16 machine screws and 2 m3 nuts.

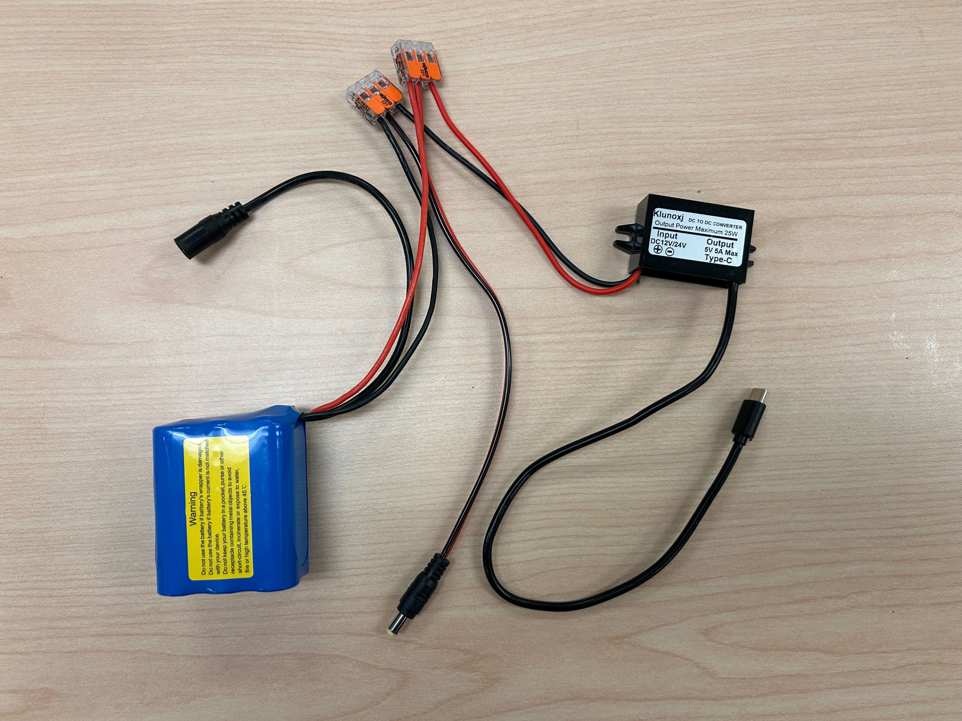
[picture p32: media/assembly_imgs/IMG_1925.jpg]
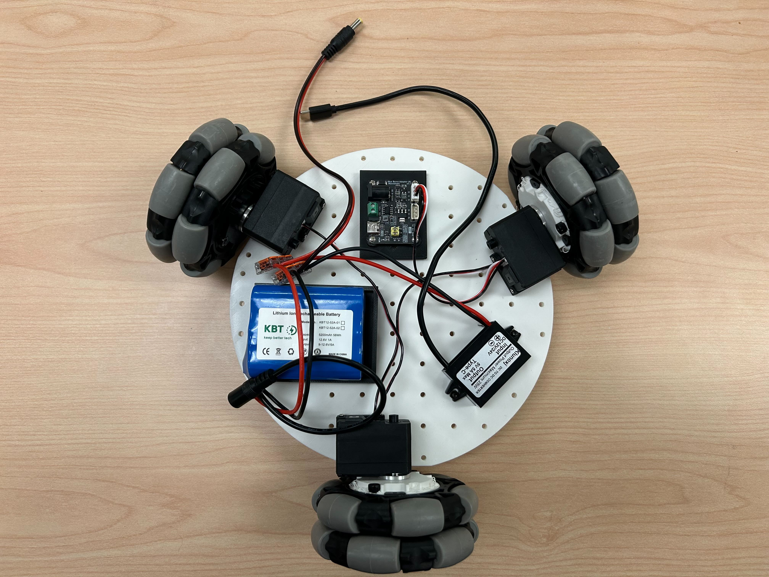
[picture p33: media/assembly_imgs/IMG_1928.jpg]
         

    - For the **5V version**: you can use the powerbamk holder to keep the powerbank in place `3DPrintMeshes/5v_specific/5v_power_bank_holder.stl`. The powerbank can be mounted in the back on the lower plate.

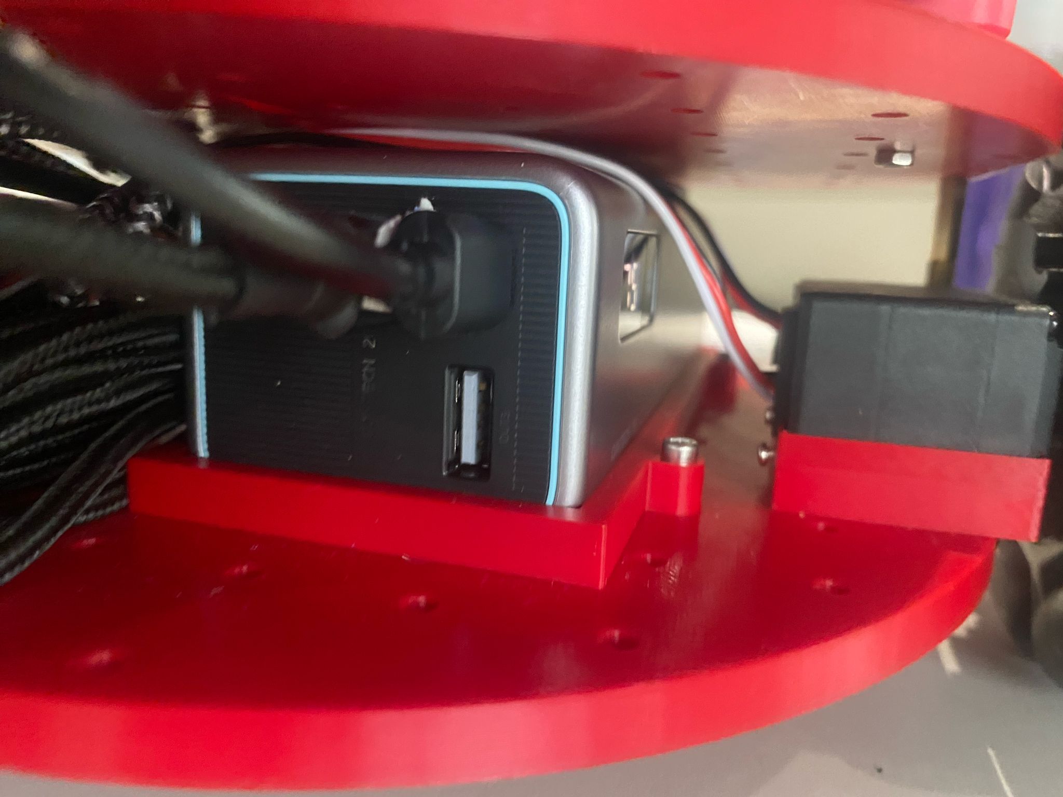
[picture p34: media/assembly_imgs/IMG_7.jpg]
        
        
      The cables can be connected  according to following diagram:
      
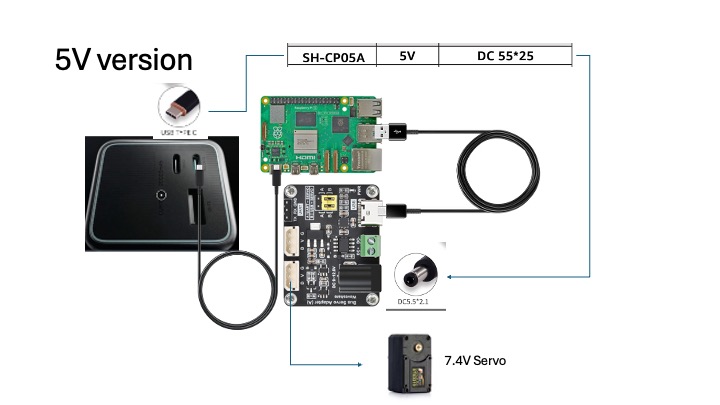
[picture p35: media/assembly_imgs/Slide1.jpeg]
        

### 3. Top plate Assembly
1. Place the raspberry pi 5 into the pi case bottom and snap on the top part of the case. 
2. Attach the Pi to the top base plate using 2 m3x12 machine screws and mount the SO-101 arm with 4 m3x20 machine screws. Using our modified SO-101 base or the original will work as there are holes for both in the plate.

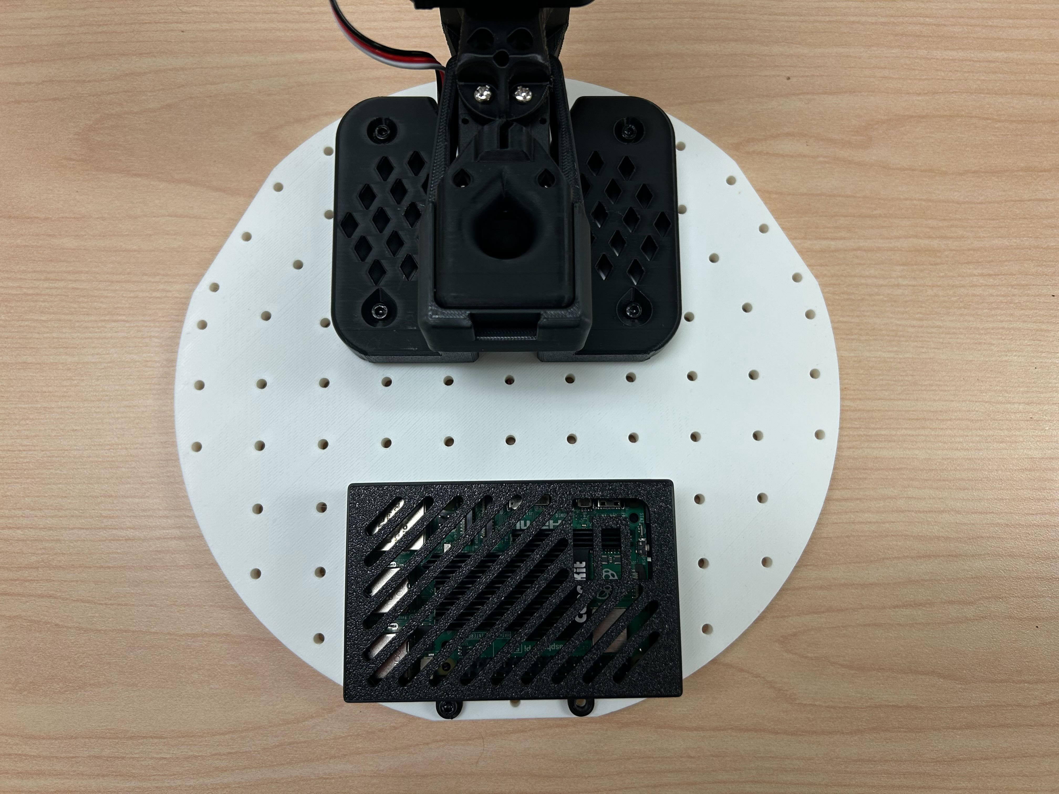
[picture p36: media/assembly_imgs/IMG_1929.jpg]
    

- For the **Wired version**: you can print these two parts: `3DPrintMeshes/wired_specific/cable_holder v0.stl` and `3DPrintMeshes/wired_specific/usb_connector_case v1.stl` and assemble them like the images below. It is **very important** to plug the usb-c cable in the way like the images. Thus the `UGreen` logo on the same side as `20GBS, 240W` logo side. And the `20GBS, 240W` side on top into your laptop. If the usb-c extenstion cable can't find your camera's or motor controller board, the cable orientation is probably wrong and should be flipped 180 degrees!

    Add cable holder and usb hub holder like this:

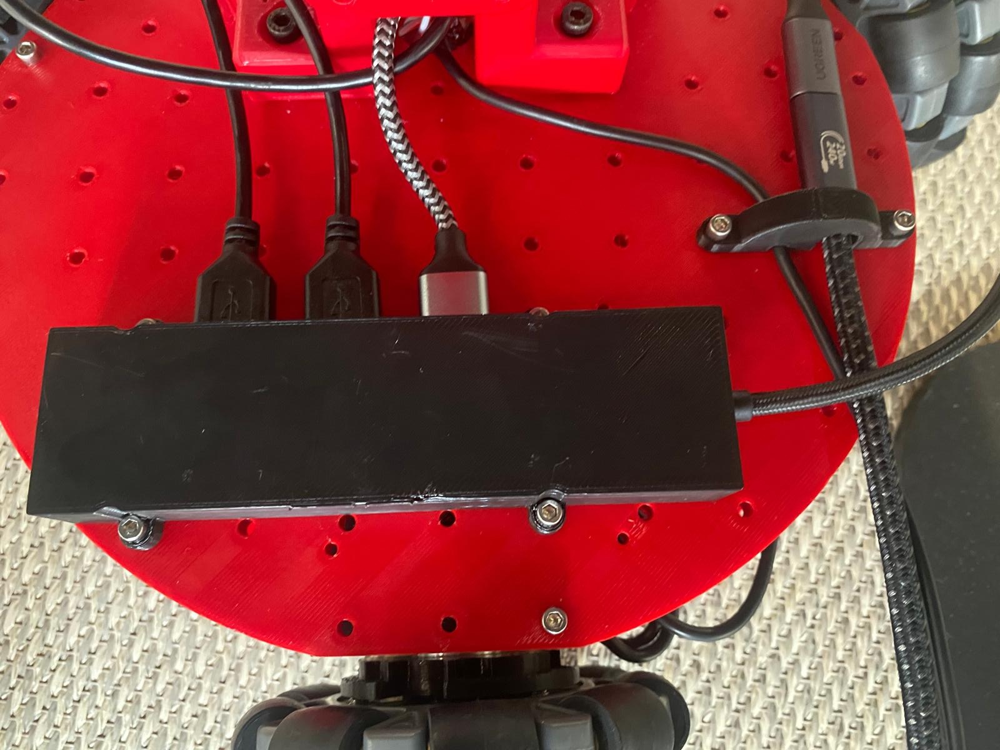
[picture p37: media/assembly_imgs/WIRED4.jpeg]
    

    Attach cables for 2 camera's motor control board and usb-c extender like this (important!):

    <div style="display: flex; align-items: flex-start;">
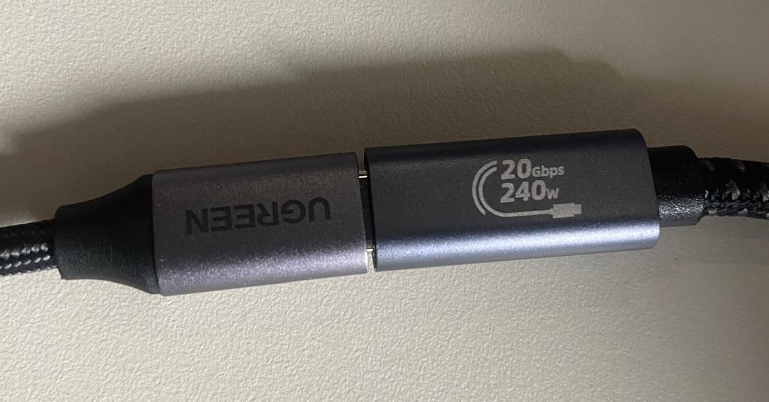
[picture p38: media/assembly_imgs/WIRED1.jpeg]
Wired Step 1
     
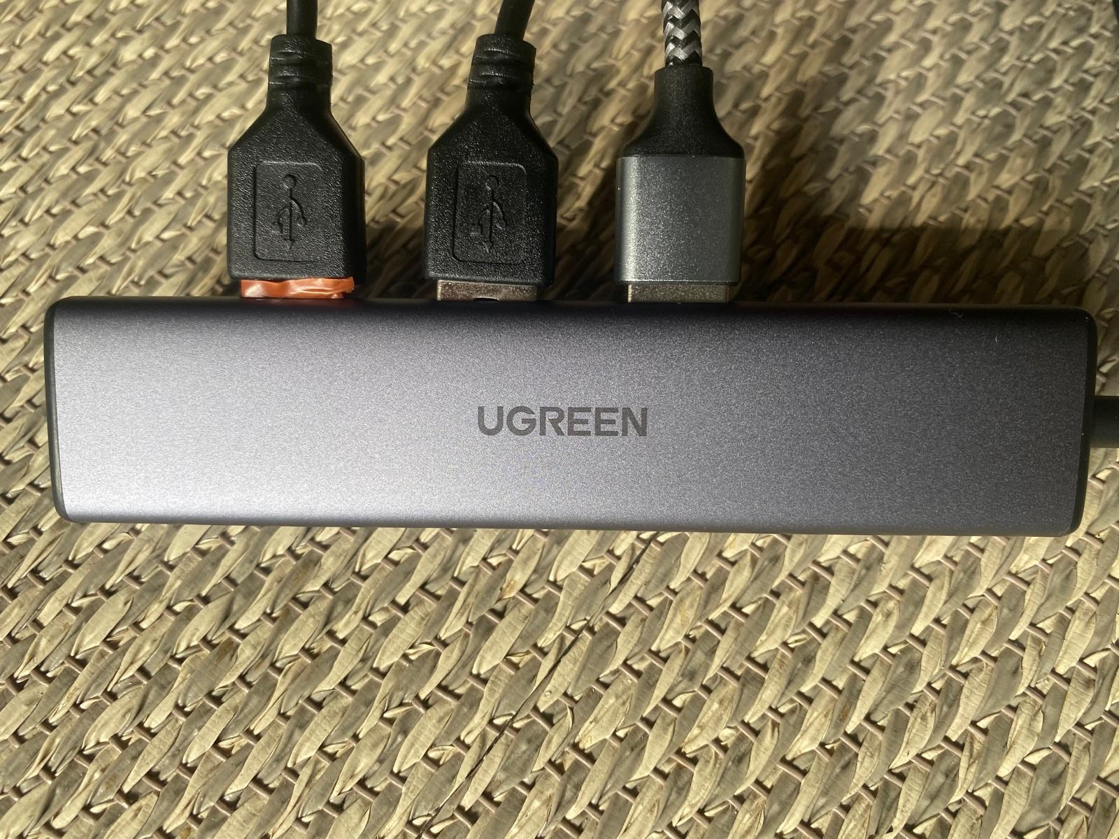
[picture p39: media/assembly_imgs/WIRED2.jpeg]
Wired Step 2
     
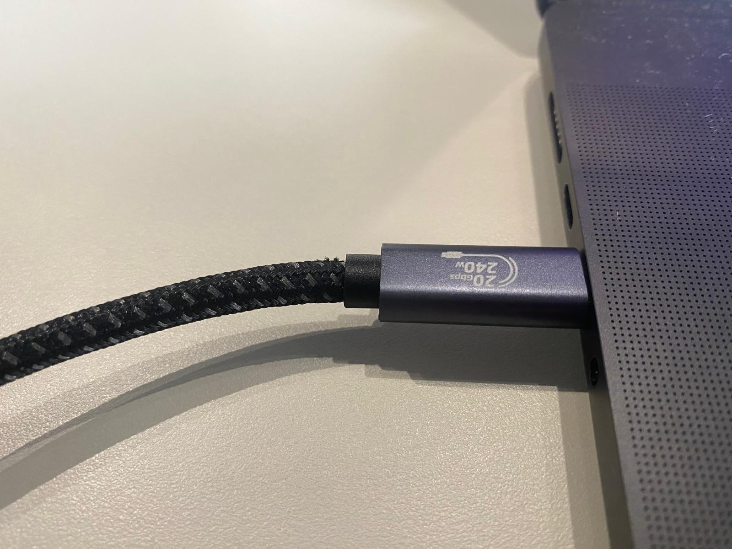
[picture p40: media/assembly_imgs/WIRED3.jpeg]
Wired Step 3
     
    </div>

### 4. Final Assembly
1. Feed the servo controller usb-c to usb-a, 5v usb-c power, and SO0-101 servo wires through the hole in the top base plate. 

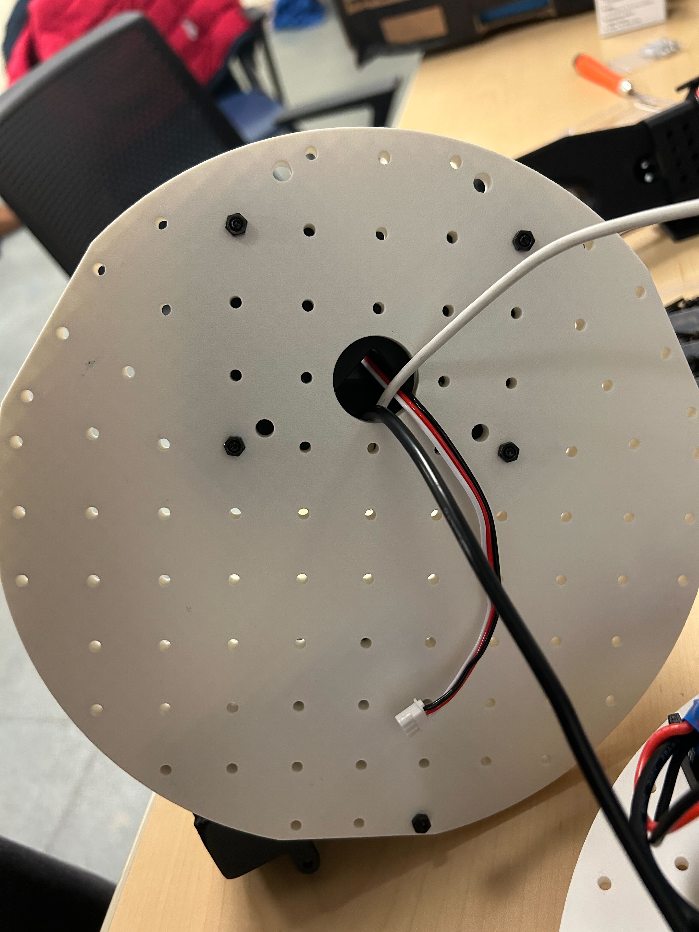
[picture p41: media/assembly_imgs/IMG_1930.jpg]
    

2. Mount the top base plate onto the motor mounts using 4 m3x12 machine screws.

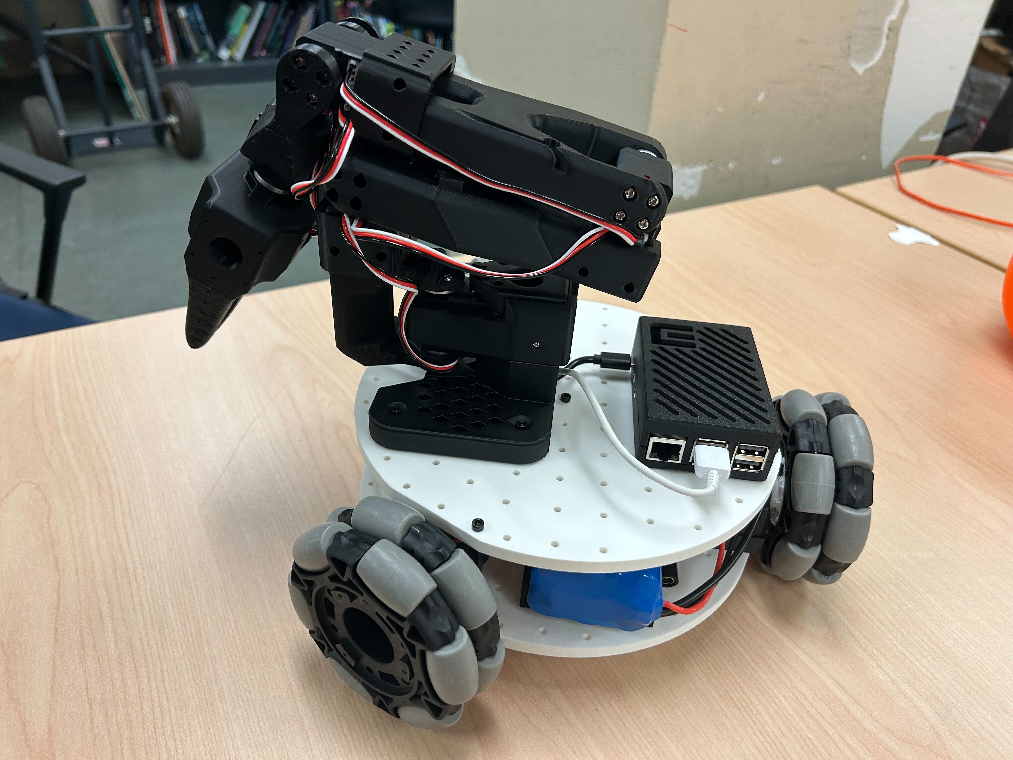
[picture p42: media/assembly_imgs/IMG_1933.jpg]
    

### 5: Attach Cameras
*Note: The mounts we designed are specific to the cameras we chose. They may need to be modified for different camera modules.*
#### (Option 1) Mounting Arducam
For these [camera's](https://www.amazon.com/Arducam-Camera-Computer-Without-Microphone/dp/B0972KK7BC) you can print these parts 1x `3DPrintMeshes/base_camera_mount.stl` and 1x `3DPrintMeshes/wrist_camera_mount.stl`.
1. Screw the base camera mount onto the bottom base plate(attach the arducam 5MP wide angle camera to the mount with 2 m2.5x12 machine screws). The cable for the camera mount can also be fed through the cutout

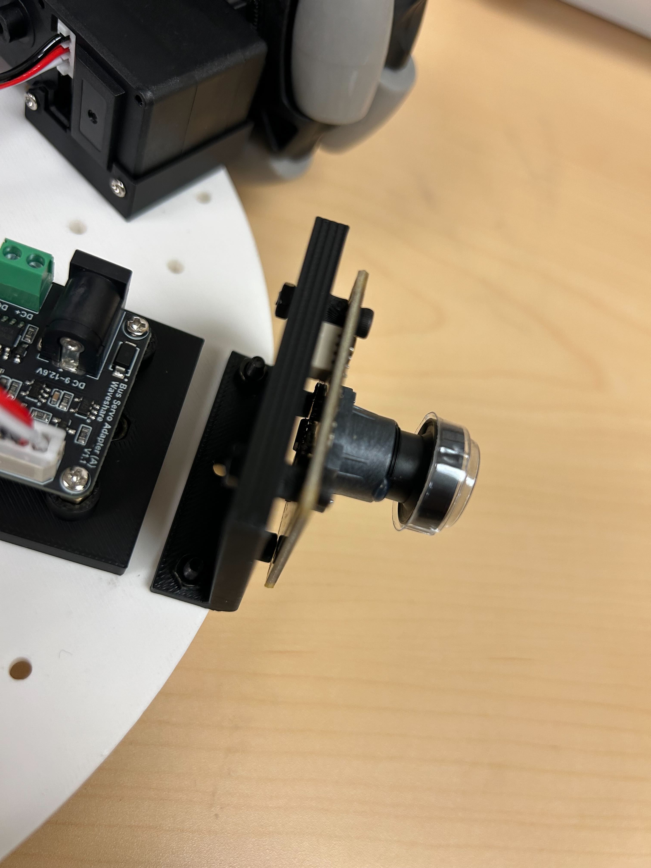
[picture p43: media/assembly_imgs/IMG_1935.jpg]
    
2. Screw the wrist camera mount to the static gripper using 4 m2x5 tap screws(attach the arducam 5MP wide angle camera to the mount with 2 m2.5x12 machine screws)

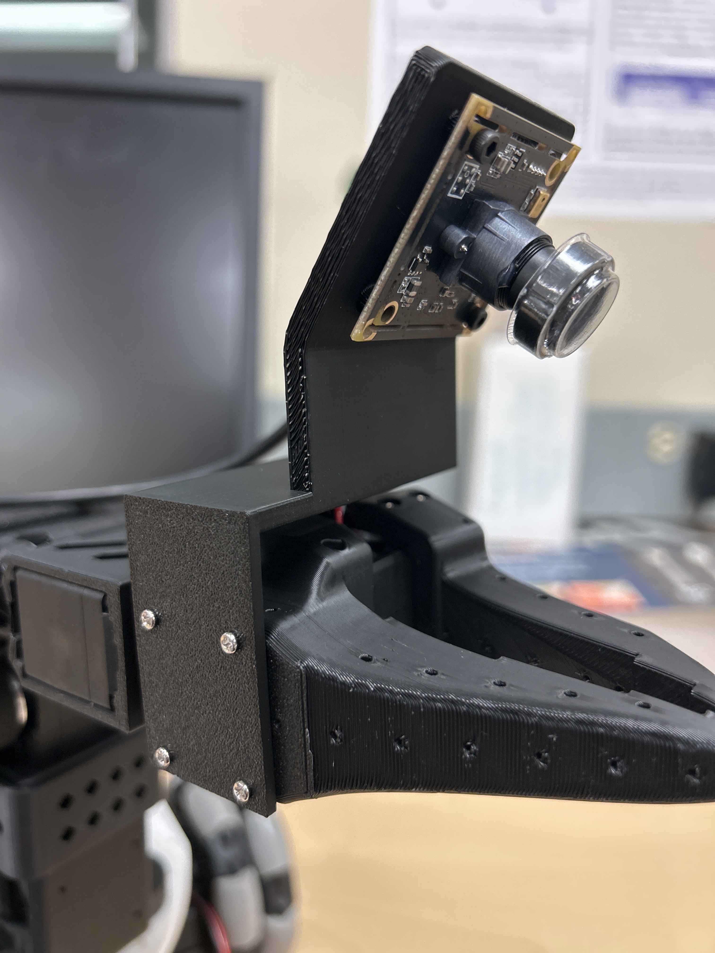
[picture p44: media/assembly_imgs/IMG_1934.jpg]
    

#### (Option 2) Mounting Webcam
For these [camera's](https://www.amazon.fr/Vinmooog-equipement-Microphone-Enregistrement-conférences/dp/B0BG1YJWFN/) you can print these parts 1x `3DPrintMeshes/webcam_mount/webcam_mount.stl`, 1x `3DPrintMeshes/webcam_mount/so100_gripper_cam_mount_insert.stl` and 1x `3DPrintMeshes/webcam_mount/webcam_mount_wrist.stl`. These can be used to attach a wrist and base camera to LeKiwi.

1. Print the new gripper with insert for the M3 nut, and insert the nut. Then insert the motor and attach gripper. 

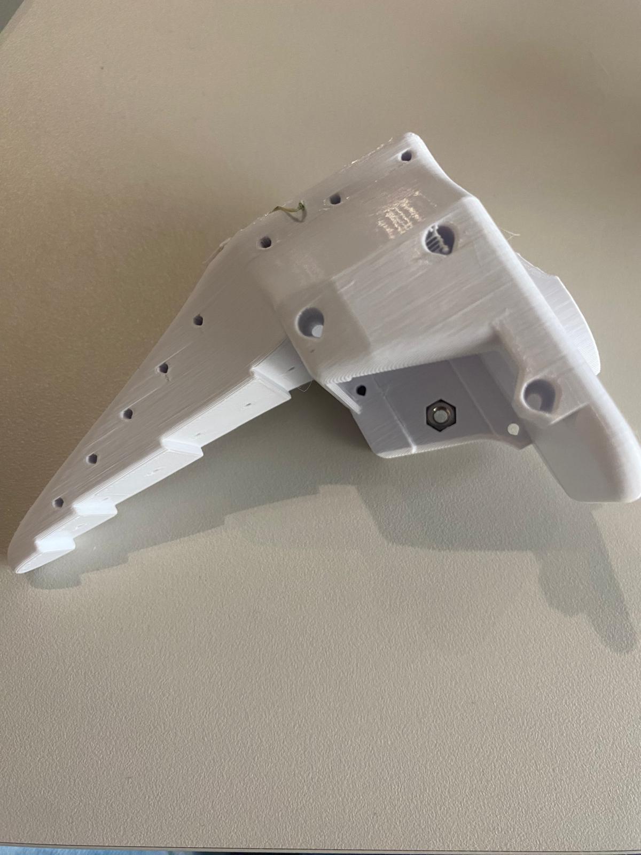
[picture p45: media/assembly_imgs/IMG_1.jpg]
    
2. Now take the camera mount `3DPrintMeshes/webcam_mount/webcam_mount_wrist.stl`, and add a M3x12mm bolt and screw it firmly until it locks with the M3 nut in the gripper. Then insert your camera in the mount and add 2x M3x35mm bolts in the back holes to lock the camera in place, use 2 nuts that you insert in the slots to lock the bolts.

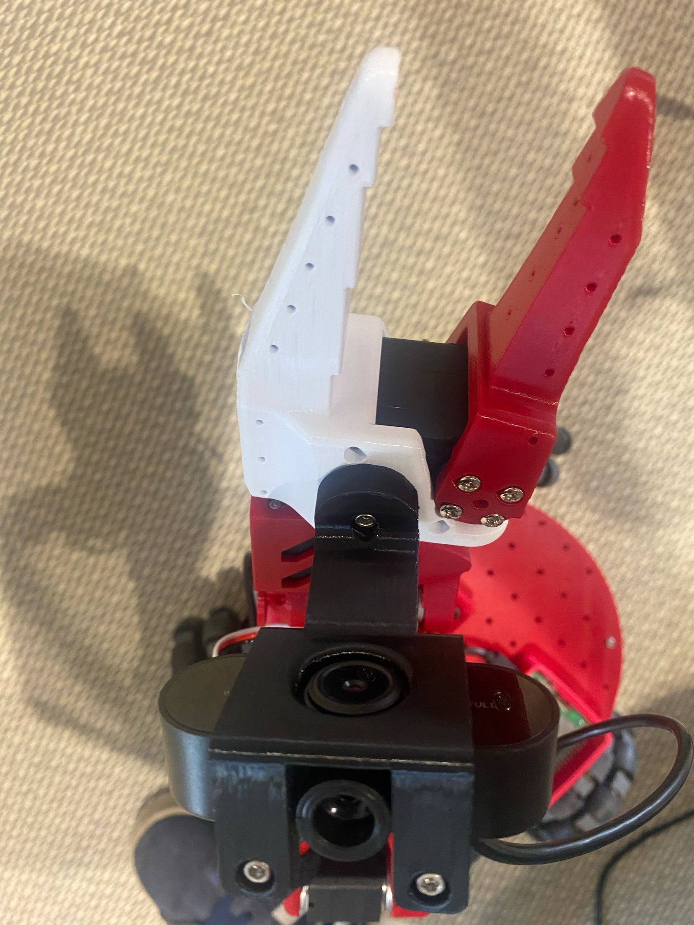
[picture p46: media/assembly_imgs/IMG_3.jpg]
    

3. Do the same for the base camera `3DPrintMeshes/webcam_mount/webcam_mount.stl` and attach it to the front of LeKiwi.

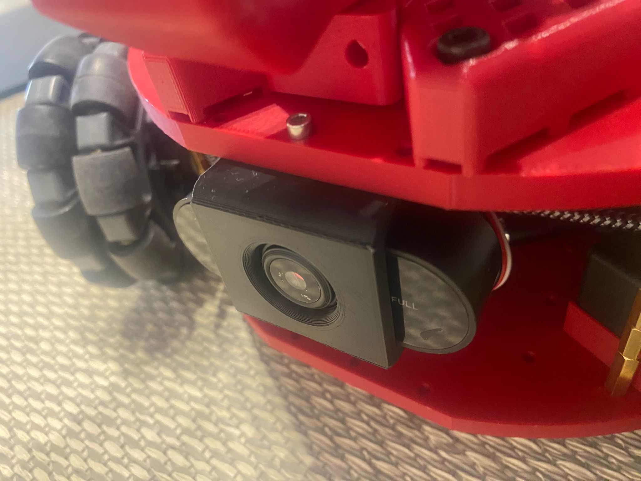
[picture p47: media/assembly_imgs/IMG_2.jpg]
    

### Plug everything in and its ready!
Power the electronics by plugging in the DC barrel plug adapter to the servo motor controller and the 5v usb-c connector to the raspberry pi 5. The usb cables from the servo controller and the cameras can directly be plugged in to the raspberry pi.

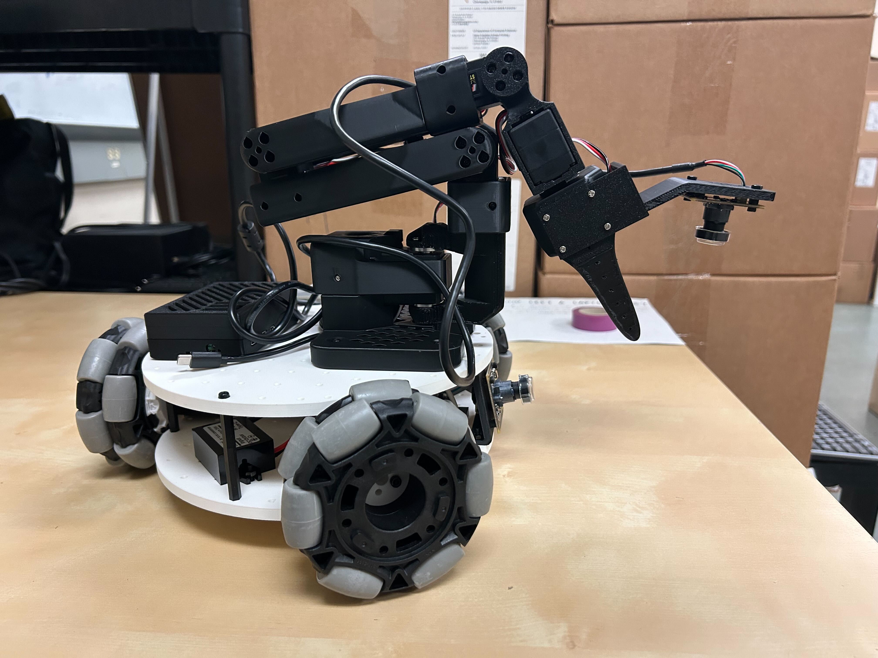
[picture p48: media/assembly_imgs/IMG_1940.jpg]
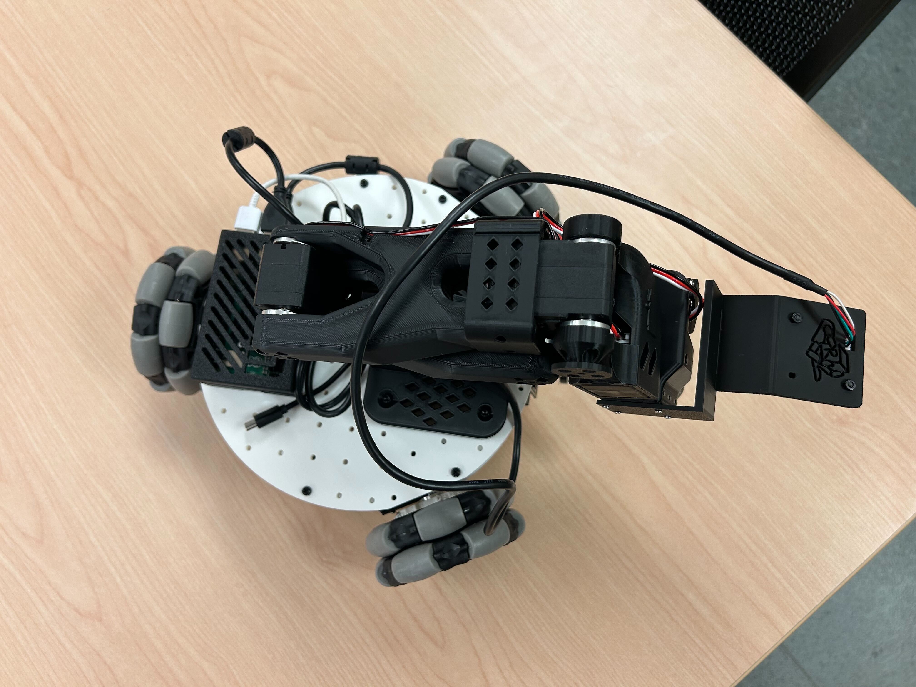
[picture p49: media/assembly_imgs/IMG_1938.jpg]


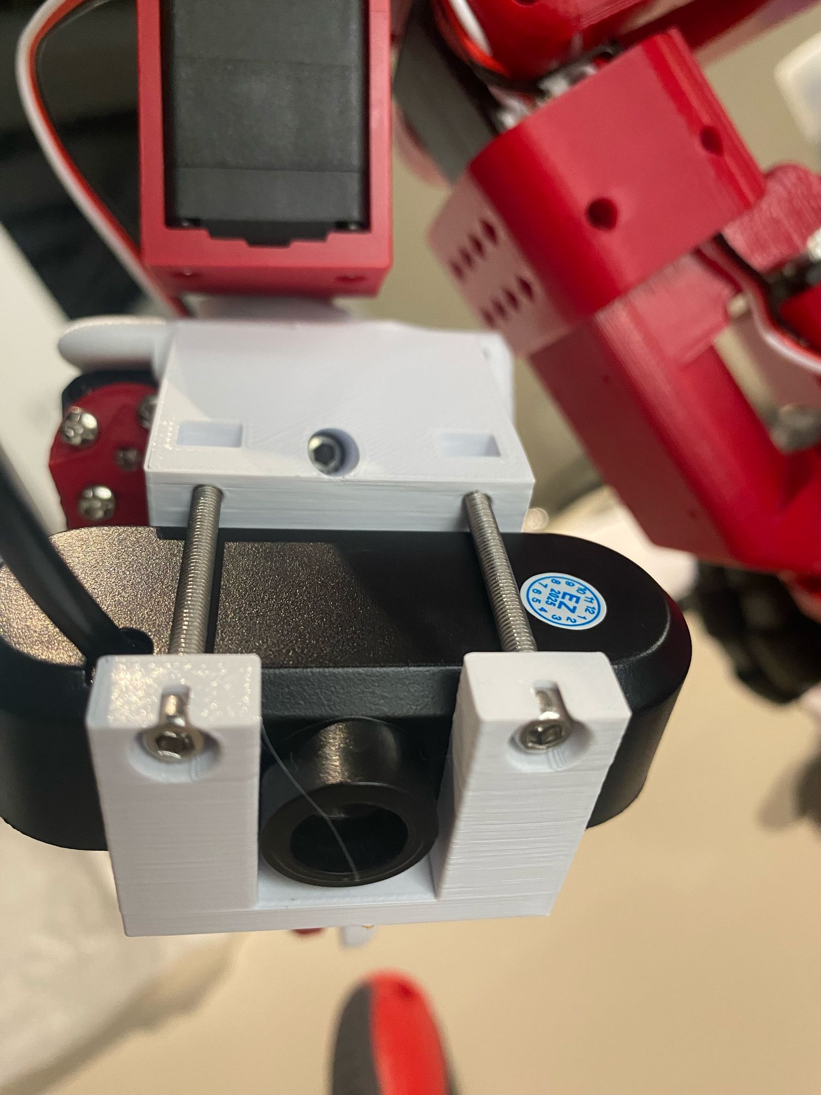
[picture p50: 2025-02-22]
media/assembly_imgs/IMG_10.jpg

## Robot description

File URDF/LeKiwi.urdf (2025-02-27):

<?xml version='1.0' encoding='utf-8'?>
<robot name="LeKiwi">
    <link name="base_plate_layer1-v5">
        <inertial>
            <origin xyz="-4.730687660675253e-15 -2.7155537377808555e-05 -0.0035000000000000005" rpy="0.0 0.0 0.0" />
            <mass value="1.9468624348344596" />
            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
        </inertial>
        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
    </link>
    <link name="drive_motor_mount-v11-2">
        <inertial>
            <origin xyz="-0.0005387977877578853 0.00013596517365616734 -0.0031122813365712966" rpy="0.0 -0.0 0.0" />
            <mass value="0.047242276734470956" />
            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
        </inertial>
        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
    </link>
    <link name="ST3215_Servo_Motor-v1-2">
        <inertial>
            <origin xyz="0.010251219185305343 -0.016877183343657672 -0.021914257028179583" rpy="0.0 -0.0 0.0" />
            <mass value="0.0658962961901927" />
            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
        </inertial>
        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
    </link>
    <link name="4-Omni-Directional-Wheel_Single_Body-v1-2">
        <inertial>
            <origin xyz="-9.805110055688405e-08 0.015875012090586064 -9.143534264177689e-08" rpy="0.0 -0.0 0.0" />
            <mass value="1.3542854082324305" />
            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
        </inertial>
        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
    </link>
    <link name="omni_wheel_mount-v5-2">
        <inertial>
            <origin xyz="5.9743256737576635e-09 -5.0148034724806225e-09 -0.005522899140934374" rpy="0.0 -0.0 0.0" />
            <mass value="0.1235708646349694" />
            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
        </inertial>
        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
    </link>
    <link name="drive_motor_mount-v11-1">
        <inertial>
            <origin xyz="0.00038715049105024767 -0.0003986280605619008 0.0031122813365712966" rpy="0.0 -0.0 0.0" />
            <mass value="0.047242276734470956" />
            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
        </inertial>
        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
    </link>
    <link name="ST3215_Servo_Motor-v1-1">
        <inertial>
            <origin xyz="0.01025121918530536 0.027816898485662264 -0.00435175717107704" rpy="0.0 -0.0 0.0" />
            <mass value="0.0658962961901927" />
            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
        </inertial>
        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
    </link>
    <link name="omni_wheel_mount-v5-1">
        <inertial>
            <origin xyz="0.004782968825905343 5.966875074037148e-09 0.0027614494161754166" rpy="0.0 -0.0 0.0" />
            <mass value="0.1235708646349694" />
            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
        </inertial>
        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
    </link>
    <link name="4-Omni-Directional-Wheel_Single_Body-v1-1">
        <inertial>
            <origin xyz="0.01374810955311503 -0.007937600014431929 -7.105207897817323e-08" rpy="0.0 -0.0 0.0" />
            <mass value="1.3542854082324305" />
            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
        </inertial>
        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
    </link>
    <link name="drive_motor_mount-v11">
        <inertial>
            <origin xyz="0.00015164729670767764 -0.0005345932342180682 -0.003112281336571299" rpy="0.0 -0.0 0.0" />
            <mass value="0.047242276734470956" />
            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
        </inertial>
        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
    </link>
    <link name="ST3215_Servo_Motor-v1">
        <inertial>
            <origin xyz="0.010251219185305386 -0.010539715142004517 0.02557319387622896" rpy="-6.077163357286271e-64 -0.0 0.0" />
            <mass value="0.0658962961901927" />
            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
        </inertial>
        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
    </link>
    <link name="omni_wheel_mount-v5">
        <inertial>
            <origin xyz="-0.00478297352513172 5.966875045171349e-09 0.002761449724759064" rpy="0.0 -0.0 0.0" />
            <mass value="0.1235708646349694" />
            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
        </inertial>
        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
    </link>
    <link name="4-Omni-Directional-Wheel_Single_Body-v1">
        <inertial>
            <origin xyz="-0.013748211804798878 -0.007937431357202592 -9.805855119449092e-08" rpy="0.0 1.0947644252537633e-47 6.865185903486632e-63" />
            <mass value="1.3542854082324305" />
            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
        </inertial>
        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
    </link>
    <link name="servo_controller_mount-v3">
        <inertial>
            <origin xyz="-2.072913100236695e-30 -3.385736135896877e-14 0.0031621761491414137" rpy="0.0 -0.0 0.0" />
            <mass value="0.12559881449596652" />
            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
        </inertial>
        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
    </link>
    <link name="lipo_battery_mount-v3">
        <inertial>
            <origin xyz="-0.008318729060206734 -4.4408920985006264e-17 -0.0046380028574369405" rpy="0.0 -0.0 0.0" />
            <mass value="0.2984320446179905" />
            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
        </inertial>
        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
    </link>
    <link name="Battery---Battery-5.2-Ah-DC5521-Plug-v2">
        <inertial>
            <origin xyz="-7.797576827959673e-05 -8.300646300726023e-05 0.020000000000000004" rpy="0.0 -0.0 0.0" />
            <mass value="1.2215469988184764" />
            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
        </inertial>
        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
    </link>
    <link name="94868A713_NO-THREADS_Female-Threaded-Hex-Standoff">
        <inertial>
            <origin xyz="2.1864399078485972e-14 1.2010287410706806e-09 -0.02499999330297986" rpy="0.0 -0.0 0.0" />
            <mass value="0.006150070863406618" />
            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
        </inertial>
        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
    </link>
    <link name="base_plate_layer2-v3">
        <inertial>
            <origin xyz="1.4406667835883843e-14 -0.000737848116891558 0.0034999999999999966" rpy="0.0 -0.0 0.0" />
            <mass value="1.9153836917607525" />
            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
        </inertial>
        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
    </link>
    <link name="Bottom-V2-v3">
        <inertial>
            <origin xyz="0.021623799145011228 0.034248555702746215 0.002860022373659428" rpy="0.0 -0.0 0.0" />
            <mass value="0.14588862570926195" />
            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
        </inertial>
        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
    </link>
    <link name="Top-V2-v2">
        <inertial>
            <origin xyz="0.00394392416615524 -0.00045096335632409 0.021552698750372336" rpy="0.0 -0.0 0.0" />
            <mass value="0.1256590419653392" />
            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
        </inertial>
        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
    </link>
    <link name="Camera-Mount-v8">
        <inertial>
            <origin xyz="-0.019889007343132665 0.003162253231103023 0.020248493842242046" rpy="0.0 -0.0 0.0" />
            <mass value="0.09265469509875414" />
            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
        </inertial>
        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
    </link>
    <link name="Camera-Model-v3">
        <inertial>
            <origin xyz="-0.01552129548236823 0.006733132771749837 -0.011599583774026805" rpy="0.0 2.7755575615628914e-17 0.0" />
            <mass value="0.039920058315088616" />
            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
        </inertial>
        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
    </link>
    <link name="Base_08q-v1">
        <inertial>
            <origin xyz="-0.03999704723368316 -0.03974905501648025 0.021865523723532104" rpy="0.0 -0.0 0.0" />
            <mass value="1.2829039880853146" />
            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
        </inertial>
        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
    </link>
    <link name="WaveShare_Mounting_Plate_01d-v1">
        <inertial>
            <origin xyz="-0.0036802122213187593 -0.0036094977362838856 6.824776544718247e-06" rpy="0.0 -0.0 0.0" />
            <mass value="0.07141322001638221" />
            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
        </inertial>
        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
    </link>
    <link name="Rotation_Pitch_08i-v1">
        <inertial>
            <origin xyz="0.00027157225787806426 -0.03155586567874573 0.009540449649933115" rpy="4.3790577010150533e-47 4.379057701015054e-47 -1.5557538194652858e-61" />
            <mass value="0.5385469320676795" />
            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
        </inertial>
        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
    </link>
    <link name="STS3215_03a-v1">
        <inertial>
            <origin xyz="-0.010249997314858655 0.016027064924721765 -0.019999026815617257" rpy="0.0 -0.0 0.0" />
            <mass value="0.2843033831904074" />
            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
        </inertial>
        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
    </link>
    <link name="SO_ARM100_08k_Asym_Mirror_Clip-v1">
        <inertial>
            <origin xyz="-0.023249790543467236 0.009494231975835899 0.002658209837920218" rpy="0.0 -0.0 0.0" />
            <mass value="0.10853073755546007" />
            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
        </inertial>
        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
    </link>
    <link name="Passive_Horn_01-v1">
        <inertial>
            <origin xyz="2.6917174546039143e-09 -0.0010740097666846627 -7.475931163014593e-10" rpy="0.0 -0.0 0.0" />
            <mass value="0.00454511487954422" />
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

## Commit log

2025-02-05 BOM updates
2025-02-05 added meshes from lcmm_mujoco
    [3_8-Hex-Bore-Plastic-VersaHub-217-5828-v2-1.stl, 3_8-Hex-Bore-Plastic-VersaHub-217-5828-v2-2.stl, 3_8-Hex-Bore-Plastic-VersaHub-217-5828-v2.stl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]
2025-02-06 updated bom
2025-02-19 updated BOM for V1
2025-02-19 update usb-c cable on bom
2025-02-19 deleted old cad meshes
    [3_8-Hex-Bore-Plastic-VersaHub-217-5828-v2-1.stl, 3_8-Hex-Bore-Plastic-VersaHub-217-5828-v2-2.stl, 3_8-Hex-Bore-Plastic-VersaHub-217-5828-v2.stl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]
2025-02-20 assembly rough draft
2025-02-21 screw size updates
2025-02-21 updated cad
2025-02-21 Add files via upload
    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
2025-02-21 Updated assembly and minor tweaks to readme and 3d print guide
    [battery_mount.stl, servo_wheel_hub.stl, wrist_camera_mount.stl]
2025-02-21 Update BOM EU and 5V version
2025-02-21 Add camera mount and battery holder 5v
    [5v_power_bank_holder.stl, so_100_gripper_with_cam_mount.stl, webcam_mount.stl]
2025-02-22 Add wrist cam update
    [so100_gripper_cam_mount_insert.stl, so_100_gripper_with_cam_mount.stl, webcam_mount_wrist.stl]
2025-02-22 12v5v version organization, Camera updates, and typos
2025-02-23 add usbc to dc cable
2025-02-25 replaced recommended cable
2025-02-27 Add URDF
    [94868A713_NO-THREADS_Female-Threaded-Hex-Standoff-1.stl, 94868A713_NO-THREADS_Female-Threaded-Hex-Standoff-2.stl, 94868A713_NO-THREADS_Female-Threaded-Hex-Stan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]
2025-02-28 3d printing updates
    [modified_base_arm.stl]
2025-03-04 Add wired version
2025-03-04 add wired assembly instructions
    [cable_holder v0.stl, usb_connector_case v1.stl]
2025-03-04 added us usb-c ext to bom
2025-03-05 Update sd card US, BOM.md
2025-03-08 add new webcam mount
    [webcam_mount.step, webcam_mount.stl, webcam_mount_wrist.step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]
2025-03-25 Add cable, recalculate prices
2025-03-25 Add diagram for the 5V version
2025-03-26 Add 5V diagram to assembly images
2025-03-26 Added 5V diagram to assembly document
2025-03-27 drive motor holder v2
    [drive_motor_mount_v2.stl]
2025-03-28 modified motor mount screw holes
    [drive_motor_mount_v2.stl]
2025-04-01 removed standoffs from BOM
2025-04-01 new motor mounts assembly update
2025-04-01 fixed case-sensitive extensions
2025-04-14 add eu 12V battery mount, and changed EU 12V battery
    [battery_mount_eu.stl]
2025-04-28 adapt base plate for so101
    [base_plate_layer2.stl]
2025-05-20 Add holder for Jetson nano
    [Jetson holder.stl]
2025-05-20 Rename Jetson holder.stl to jetson_holder.stl
    [jetson_holder.stl]
